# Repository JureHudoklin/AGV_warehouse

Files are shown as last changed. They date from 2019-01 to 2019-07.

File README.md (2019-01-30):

# AGV_warehouse

This is a project I am currently working on. I am working on this also as a final project for my undergraduate degree (diploma). In this project I am developing and programing a robot ("robot platform") that could be used in simulation of a warehouse environment. In a simulation these robots would have to found their way around warehouse based on the input provided by the master computer. Each robot has to follow guiding lines, know his position based on ground markings, be able to autonomously charge itself, stop and report in case of obstacles and load cargo from designated stations. 

I already completed the robot design phase. I have designed the pcb plate as well as the whole assembly. The robot will be assembled in next few weeks when I receive all the necessary parts. This part of the project is located in ./agv-skladiscni-v1/ (KiCad files) and ./Step_modeli/ (step models of robot and pcb plate).

The logic of the robot will run on a BeagleBone blue board. The board will run a ROS operating system. This is the part I have just started working on. I am writing the code in C++ which is the first bigger program I am writing in C++. I expect to learn C++ quite well when I am finished with this project. The code part of this project can be found in the ./catkin_ws/src/ folder. I have not written a lot of code yet bet the currently working part is locate in robot_control package 

**./catkin_ws/src/robot_control/src/...**

<image src="robot_v4/step_modeli/robot_picture.jpg">

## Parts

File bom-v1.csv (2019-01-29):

Refs | Value | Footprint | Quantity | MFR | MPN | SPR | SPN
J4 | I2C | Connector_Wire:SolderWirePad_1x04_P3.175mm_Drill0.8mm | 1 | - | - | - | -
J1 | TOF_0 | Connector_Wire:SolderWirePad_1x05_P3.175mm_Drill0.8mm | 1 | - | - | - | -
J2 | TOF_1 | Connector_Wire:SolderWirePad_1x05_P3.175mm_Drill0.8mm | 1 | - | - | - | -
J5 | ADC | Connector_Wire:SolderWirePad_2x03_P3.175mm_Drill0.8mm | 1 | - | - | - | -
J6 | GP0 | Connector_Wire:SolderWirePad_2x03_P3.175mm_Drill0.8mm | 1 | - | - | - | -
J3 | GP1 | Connector_Wire:SolderWirePad_2x03_P3.175mm_Drill0.8mm | 1 | - | - | - | -
IC1;IC2 | NLAST4051DTR2G | NLAST4051DTR2G:SOP65P640X120-16N | 2 |  | -NLAST4051DTR2G | - | -
U3;U4;U7;U8;U11;U12;U15;U16;U1;U2;U5;U6;U9;U10;U13;U14 | QRE1113GR | OptoDevice:Everlight_ITR8307F43 | 16 | - | -QRE1113GR | - | -
Q1;Q2 | BSS138 | Package_TO_SOT_SMD:SOT-23 | 2 | - | -BSS138 | - | -
R4;R6;R10;R12;R16;R21;R26;R28;R3;R5;R9;R11;R15;R20;R25;R27;R29;R30;R17;R18;R19;R22 | 10K | Resistor_SMD:R_0805_2012Metric_Pad1.15x1.40mm_HandSolder | 22 | - | -CRCW080510K0FKEAC | - | -
R2;R8;R14;R24;R1;R7;R13;R23 | 35R | Resistor_SMD:R_0805_2012Metric_Pad1.15x1.40mm_HandSolder | 8 | - | -ERJ-6ENF35R7V | - | -

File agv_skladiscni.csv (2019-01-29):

Qty | Line Item | Manufacturer | MPN | Octopart URL | Schematic Reference | Internal Part Number | Description | Total Qty (@ Batch Size: 1) | SKU | SKU | SKU | Packaging | Packaging | Packaging | Unit Price (@ Batch Size: 1) | Unit Price (@ Batch Size: 1) | Unit Price (@ Batch Size: 1) | In Stock | In Stock | In Stock | MOQ | MOQ | MOQ | URL | URL | URL | Distributor [Custom] | SKU [Custom] | Packaging [Custom] | Unit Price (@ Batch Size: 1) [Custom] | Line Total [Custom] | Batch Total [Custom] | In Stock [Custom] | MOQ [Custom] | URL [Custom] | Notes
 |  |  |  |  |  |  |  |  | Digi-Key | Arrow Electronics, Inc. | Mouser | Digi-Key | Arrow Electronics, Inc. | Mouser | Digi-Key | Arrow Electronics, Inc. | Mouser | Digi-Key | Arrow Electronics, Inc. | Mouser | Digi-Key | Arrow Electronics, Inc. | Mouser | Digi-Key | Arrow Electronics, Inc. | Mouser
2 | '-NLAST4051DTR2G | ON Semiconductor | NLAST4051DTR2G | https://octopart.com/nlast4051dtr2g-on+semiconductor-445224 |  |  |  | 2 | NLAST4051DTR2GOSCT-ND | NLAST4051DTR2G | NLAST4051DTR2G | Cut Tape | Cut Tape |  | 0.82028697 | 0.4874974282999999 | 0.8026463899999999 | 211 | 1 | 1261 | 1 | 1 | 1 | https://octopart.com/click/track?ak=68b25f31&sig=00cf630&sid=459&ppid=445224&vpid=34062617&ct=offers | https://octopart.com/click/track?ak=68b25f31&sig=09833bd&sid=1106&ppid=445224&vpid=473373786&ct=offers | https://octopart.com/click/track?ak=68b25f31&sig=00e537d&sid=2401&ppid=445224&vpid=116317130&ct=offers | Farnell | 2464612 | Cut Tape | 0.641 | 1.282 | 1.282 | 3755 | 1 | https://octopart.com/click/track?ak=68b25f31&sig=0dc249f&sid=819&ppid=445224&vpid=206199120&ct=offers
16 | QRE1113 | ON Semiconductor | QRE1113 | https://octopart.com/qre1113-on+semiconductor-84331128 |  |  |  | 16 | QRE1113-ND | QRE1113 | QRE1113 | Tube |  |  | 0.792062042 | 0.5158105592 | 0.682690446 | 10991 | 646 | 3394 | 1 | 1 | 1 | https://octopart.com/click/track?ak=68b25f31&sig=0a14e08&sid=459&ppid=84331128&vpid=452472821&ct=offers | https://octopart.com/click/track?ak=68b25f31&sig=092d03a&sid=1106&ppid=84331128&vpid=451899349&ct=offers | https://octopart.com/click/track?ak=68b25f31&sig=0bf3216&sid=2401&ppid=84331128&vpid=438586711&ct=offers | Avnet | QRE1113 |  | 0.4762074571 | 7.6193193136 | 7.6193193136 | 15772 | 1 | https://octopart.com/click/track?ak=68b25f31&sig=06b2d4a&sid=5822&ppid=84331128&vpid=450368001&ct=offers
2 | BSS138 | ON Semiconductor | BSS138 | https://octopart.com/bss138-on+semiconductor-19021258 |  |  |  | 2 | BSS138CT-ND | BSS138 | BSS138 | Cut Tape |  |  | 0.27342899 |  | 0.23814783 | 814070 | 189000 | 13677 | 1 | 3000 | 1 | https://octopart.com/click/track?ak=68b25f31&sig=004b419&sid=459&ppid=19021258&vpid=452459305&ct=offers | https://octopart.com/click/track?ak=68b25f31&sig=05a773f&sid=1106&ppid=19021258&vpid=485898217&ct=offers | https://octopart.com/click/track?ak=68b25f31&sig=0af2366&sid=2401&ppid=19021258&vpid=438580598&ct=offers | ExcessParts.Net | BSS138 |  | 0.11466377 | 0.22932754 | 0.22932754 | 200 |  | https://octopart.com/click/track?ak=68b25f31&sig=03c28bd&sid=13803&ppid=19021258&vpid=81172639&ct=offers
22 | '-CRCW080510K0FKEAC | Vishay | CRCW080510K0FKEAC | https://octopart.com/crcw080510k0fkeac-vishay-23798533 |  |  |  | 22 | 541-3976-1-ND | CRCW080510K0FKEAC | CRCW080510K0FKEAC | Cut Tape | Cut Tape |  | 0.042337392 | 0.0388974789 | 0.074090436 | 2081785 | 509250 | 477454 | 1 | 1 | 1 | https://octopart.com/click/track?ak=68b25f31&sig=0d20d2d&sid=459&ppid=23798533&vpid=454353705&ct=offers | https://octopart.com/click/track?ak=68b25f31&sig=028f037&sid=1106&ppid=23798533&vpid=473524074&ct=offers | https://octopart.com/click/track?ak=68b25f31&sig=030ab9c&sid=2401&ppid=23798533&vpid=454250937&ct=offers | Arrow Electronics, Inc. | CRCW080510K0FKEAC | Cut Tape | 0.0388974789 | 0.8557445358 | 0.8557445358 | 509250 | 1 | https://octopart.com/click/track?ak=68b25f31&sig=028f037&sid=1106&ppid=23798533&vpid=473524074&ct=offers
8 | '-ERJ-6ENF35R7V | Panasonic | ERJ-6ENF35R7V | https://octopart.com/erj-6enf35r7v-panasonic-55422637 |  |  |  | 8 | P35.7CCT-ND | ERJ-6ENF35R7V | ERJ-6ENF35R7V | Cut Tape | Cut Tape |  | 0.0882029 | 0.07938260999999999 | 0.0882029 | 15875 | 4900 | 95993 | 1 | 1 | 1 | https://octopart.com/click/track?ak=68b25f31&sig=09c9812&sid=459&ppid=55422637&vpid=189121626&ct=offers | https://octopart.com/click/track?ak=68b25f31&sig=0660927&sid=1106&ppid=55422637&vpid=473401578&ct=offers | https://octopart.com/click/track?ak=68b25f31&sig=0f0ac6a&sid=2401&ppid=55422637&vpid=195943639&ct=offers | Digi-Key | P35.7CCT-ND | Cut Tape | 0.0882029 | 0.7056232 | 0.7056232 | 15875 | 1 | https://octopart.com/click/track?ak=68b25f31&sig=09c9812&sid=459&ppid=55422637&vpid=189121626&ct=offers
8 | 0854-0-15-20-82-14-11-0 | Mill-Max | 0854-0-15-20-82-14-11-0 | https://octopart.com/0854-0-15-20-82-14-11-0-mill-max-20463977 |  |  |  | 8 | ED1055-ND | 0854-0-15-20-82-14-11-0 | 0854-0-15-20-82-14-11-0 | Bulk |  | Bulk | 0.87320871 | 1.211025817 | 0.87320871 | 112317 | 526 | 0 | 1 | 1 | 1 | https://octopart.com/click/track?ak=68b25f31&sig=0a25628&sid=459&ppid=20463977&vpid=40329792&ct=offers | https://octopart.com/click/track?ak=68b25f31&sig=0bc0763&sid=1106&ppid=20463977&vpid=473313268&ct=offers | https://octopart.com/click/track?c=1&ak=68b25f31&sig=03ae4f1&sid=2401&ppid=20463977&vpid=41065394&ct=offers | Farnell | 2751174 |  | 0.702 | 5.616 | 5.616 | 111 | 1 | https://octopart.com/click/track?ak=68b25f31&sig=03bcc03&sid=819&ppid=20463977&vpid=429766510&ct=offers
1 | BBONE-BLUE | BeagleBoard | BBONE-BLUE | https://octopart.com/bbone-blue-beagleboard-81066055 |  |  |  | 1 |  |  |  |  |  |  |  |  |  |  |  |  |  |  |  |  |  |  | Farnell | 2612583 |  | 69.39 | 69.39 | 69.39 | 2492 | 1 | https://octopart.com/click/track?ak=68b25f31&sig=0b051db&sid=819&ppid=81066055&vpid=423723874&ct=offers
4 | 30:1 MICRO METAL GEARMOTOR MP 6V DUAL | Pololu | 30:1 MICRO METAL GEARMOTOR MP 6V DUAL | https://octopart.com/30%3A1+micro+metal+gearmotor+mp+6v+dual-pololu-75431235 |  |  |  | 4
2 | MICRO METAL GEARMOTOR BRACKET PAIR - WHI | Pololu | MICRO METAL GEARMOTOR BRACKET PAIR - WHI | https://octopart.com/micro+metal+gearmotor+bracket+pair+-+whi-pololu-75442825 |  |  |  | 2
8 | R2-56X3/4 | APM Hexseal | R2-56X3/4 | https://octopart.com/r2-56x3%2F4-apm+hexseal-133757 |  |  |  | 8 |  |  | R2-56X3/4 |  |  |  |  |  | 0.48511595 |  |  | 54 |  |  | 1 |  |  | https://octopart.com/click/track?ak=68b25f31&sig=062e0ba&sid=2401&ppid=133757&vpid=230952262&ct=offers | Mouser | R2-56X3/4 |  | 0.48511595 | 3.8809276 | 3.8809276 | 54 | 1 | https://octopart.com/click/track?ak=68b25f31&sig=062e0ba&sid=2401&ppid=133757&vpid=230952262&ct=offers
2 | SEN-14722 | SparkFun | SEN-14722 | https://octopart.com/sen-14722-sparkfun-93101365 |  |  |  | 2 | 1568-1880-ND | SEN-14722 | SEN-14722 | Bulk |  |  | 19.298794519999998 | 17.596478549999997 | 19.8456525 | 111 | 8 | 22 | 1 | 1 | 1 | https://octopart.com/click/track?c=1&ak=68b25f31&sig=0b0900d&sid=459&ppid=93101365&vpid=485092018&ct=offers | https://octopart.com/click/track?ak=68b25f31&sig=0332f6e&sid=1106&ppid=93101365&vpid=492168591&ct=offers | https://octopart.com/click/track?ak=68b25f31&sig=0545640&sid=2401&ppid=93101365&vpid=486713343&ct=offers | Arrow Electronics, Inc. | SEN-14722 |  | 17.596478549999997 | 35.192957099999994 | 35.192957099999994 | 8 | 1 | https://octopart.com/click/track?ak=68b25f31&sig=0332f6e&sid=1106&ppid=93101365&vpid=492168591&ct=offers
8 | 05.13.253 | Ettinger | 05.13.253 | https://octopart.com/05.13.253-ettinger-5437306 |  |  |  | 8 |  |  |  |  |  |  |  |  |  |  |  |  |  |  |  |  |  |  | element14 APAC | 1466796 |  | 0.4796423356182361 | 3.837138684945889 | 3.837138684945889 | 14871 | 4 | https://octopart.com/click/track?ak=68b25f31&sig=056c70d&sid=11744&ppid=5437306&vpid=132270724&ct=offers
4 | 05.12.103 | Ettinger | 05.12.103 | https://octopart.com/05.12.103-ettinger-5415987 |  |  |  | 4 |  |  |  |  |  |  |  |  |  |  |  |  |  |  |  |  |  |  | element14 APAC | 1466834 |  | 0.28778540137094166 | 1.1511416054837667 | 1.1511416054837667 | 10290 | 4 | https://octopart.com/click/track?ak=68b25f31&sig=01c4ea7&sid=11744&ppid=5415987&vpid=132270698&ct=offers
4 | M2.5 6 PRSTMC Z100 | TR Fastenings | M2.5 6 PRSTMC Z100 | https://octopart.com/m2.5+6+prstmc+z100-tr+fastenings-95659952 |  |  |  | 4 |  |  |  |  |  |  |  |  |  |  |  |  |  |  |  |  |  |  | Farnell | 1420388 |  | 1.17 | 4.68 | 4.68 | 634 | 1 | https://octopart.com/click/track?ak=68b25f31&sig=0602cf9&sid=819&ppid=95659952&vpid=509078641&ct=offers
8 | M3 12 PRSTMC Z100 | TR Fastenings | M3 12 PRSTMC Z100 | https://octopart.com/m3+12+prstmc+z100-tr+fastenings-95659955 |  |  |  | 8 |  |  |  |  |  |  |  |  |  |  |  |  |  |  |  |  |  |  | Farnell | 1420391 |  | 1.24 | 9.92 | 9.92 | 1097 | 1 | https://octopart.com/click/track?ak=68b25f31&sig=05d7318&sid=819&ppid=95659955&vpid=509078647&ct=offers
20 | M3- HFST-Z100- | TR Fastenings | M3- HFST-Z100- | https://octopart.com/m3-+hfst-z100--tr+fastenings-7394229 |  |  |  | 20 |  |  |  |  |  |  |  |  |  |  |  |  |  |  |  |  |  |  | Farnell | 1419447 |  | 0.977 | 19.54 | 19.54 | 3192 | 1 | https://octopart.com/click/track?ak=68b25f31&sig=02b8b90&sid=819&ppid=7394229&vpid=509078655&ct=offers
4 | M2.5- HFST-Z100- | TR Fastenings | M2.5- HFST-Z100- | https://octopart.com/m2.5-+hfst-z100--tr+fastenings-7512629 |  |  |  | 4 |  |  |  |  |  |  |  |  |  |  |  |  |  |  |  |  |  |  | Farnell | 1419446 |  | 1.01 | 4.04 | 4.04 | 1228 | 1 | https://octopart.com/click/track?ak=68b25f31&sig=06cf466&sid=819&ppid=7512629&vpid=509078643&ct=offers
4 | DT000386 | Duratool | DT000386 | https://octopart.com/dt000386-duratool-89505181 |  |  |  | 4 |  |  |  |  |  |  |  |  |  |  |  |  |  |  |  |  |  |  | Newark | 48AC6552 |  | 5.16868994 | 20.67475976 | 20.67475976 | 28 | 1 | https://octopart.com/click/track?ak=68b25f31&sig=0d0659c&sid=2402&ppid=89505181&vpid=477436522&ct=offers
0 | 212X10 | Dremec | 212X10 | https://octopart.com/212x10-dremec-53597534 |  |  |  | 0 |  |  |  |  |  |  |  |  |  |  |  |  |  |  |  |  |  |  | TME | TFM-M2.5X10/DR212 |  |  |  |  | 3170 | 10 | https://octopart.com/click/track?ak=68b25f31&sig=0ad5945&sid=1532&ppid=53597534&vpid=180689506&ct=offers
0 | 213X25 | Dremec | 213X25 | https://octopart.com/213x25-dremec-53597544 |  |  |  | 0 |  |  |  |  |  |  |  |  |  |  |  |  |  |  |  |  |  |  | TME | TFM-M3X25/DR213 |  |  |  |  | 12040 | 10 | https://octopart.com/click/track?ak=68b25f31&sig=0f4a038&sid=1532&ppid=53597544&vpid=180689516&ct=offers
0 | 1874659 | Bossard | 1874659 | https://octopart.com/1874659-bossard-20924902 |  |  |  | 0 |  |  |  |  |  |  |  |  |  |  |  |  |  |  |  |  |  |  | TME | B3/BN117 |  |  |  |  | 245493 | 100 | https://octopart.com/click/track?ak=68b25f31&sig=0f10d11&sid=1532&ppid=20924902&vpid=195120838&ct=offers
0 | M2.5/BN109 | Bossard | M2.5/BN109 | https://octopart.com/m2.5%2Fbn109-bossard-30715687 |  |  |  | 0 |  |  |  |  |  |  |  |  |  |  |  |  |  |  |  |  |  |  | TME | B2.5/BN109 |  |  |  |  | 38815 | 100 | https://octopart.com/click/track?ak=68b25f31&sig=06c4eca&sid=1532&ppid=30715687&vpid=88509478&ct=offers
0 | 1154273 | Bossard | 1154273 | https://octopart.com/1154273-bossard-30713602 |  |  |  | 0 |  |  |  |  |  |  |  |  |  |  |  |  |  |  |  |  |  |  | TME | B3X12/BN384 |  |  |  |  | 8200 | 200 | https://octopart.com/click/track?ak=68b25f31&sig=0083844&sid=1532&ppid=30713602&vpid=88491571&ct=offers
0 | 1135716 | Bossard | 1135716 | https://octopart.com/1135716-bossard-30713551 |  |  |  | 0 |  |  |  |  |  |  |  |  |  |  |  |  |  |  |  |  |  |  | TME | B3X40/BN384 |  |  |  |  | 3200 | 200 | https://octopart.com/click/track?ak=68b25f31&sig=017a52f&sid=1532&ppid=30713551&vpid=88490955&ct=offers
0 | 1154192 | Bossard | 1154192 | https://octopart.com/1154192-bossard-30713592 |  |  |  | 0 |  |  |  |  |  |  |  |  |  |  |  |  |  |  |  |  |  |  | TME | B2.5X6/BN384 |  |  |  |  | 3200 | 200 | https://octopart.com/click/track?ak=68b25f31&sig=060e8c5&sid=1532&ppid=30713592&vpid=88491441&ct=offers

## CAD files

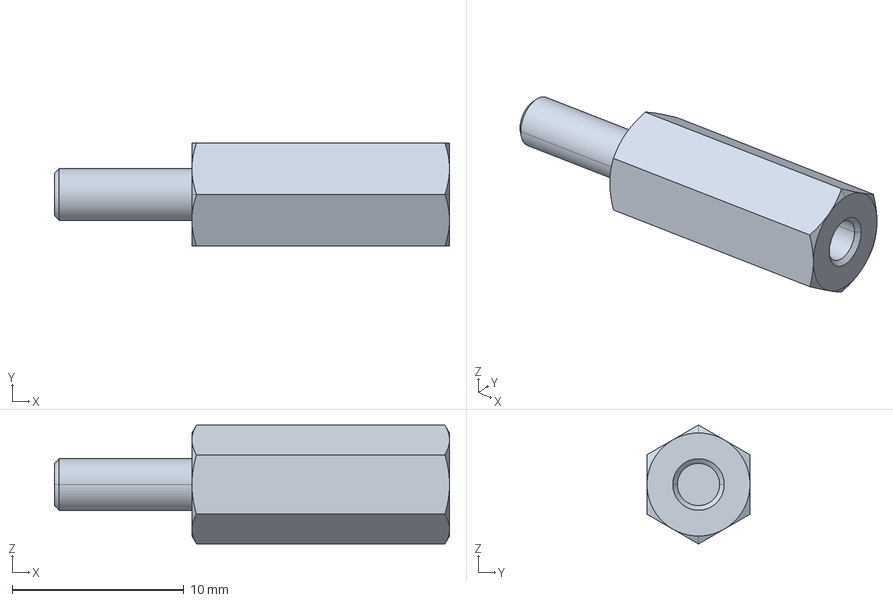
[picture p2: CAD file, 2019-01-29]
robot_v4/step_modeli/pillar_210630060015.stp
23.0 x 6.00 x 6.93 mm

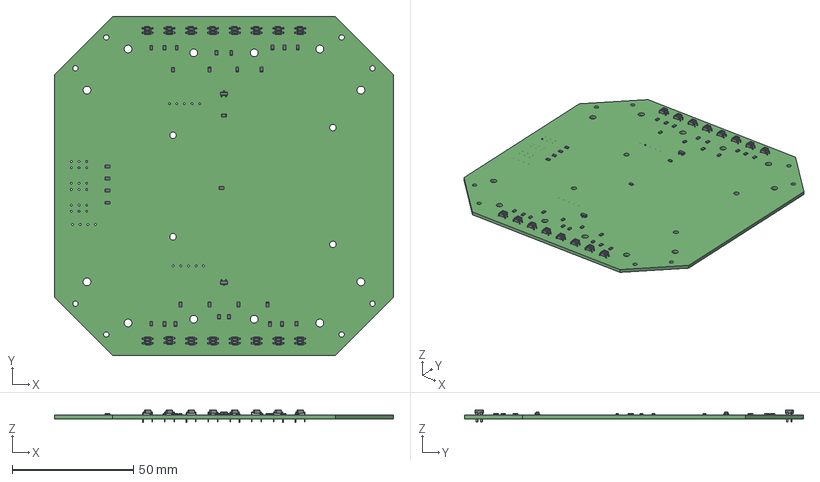
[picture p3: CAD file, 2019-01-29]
robot_v4/step_modeli/agv-skladiscni-v5.step
140.0 x 140.0 x 5.00 mm

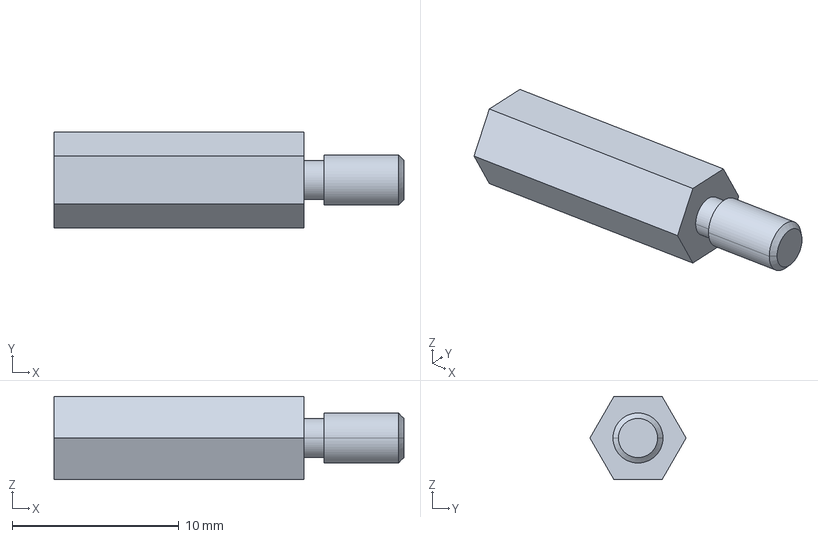
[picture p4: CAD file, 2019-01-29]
robot_v4/step_modeli/yp-515.stp
21.0 x 5.77 x 5.00 mm

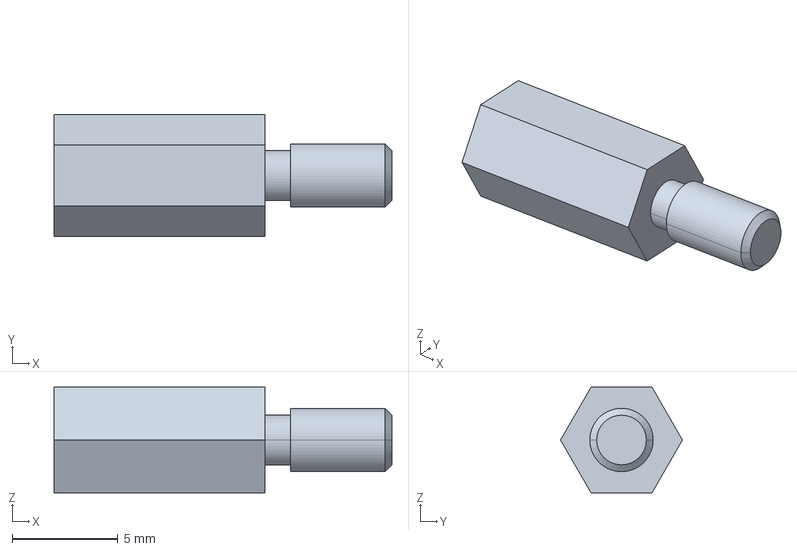
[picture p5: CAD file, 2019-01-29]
robot_v4/step_modeli/yp-510.stp
16.0 x 5.77 x 5.00 mm

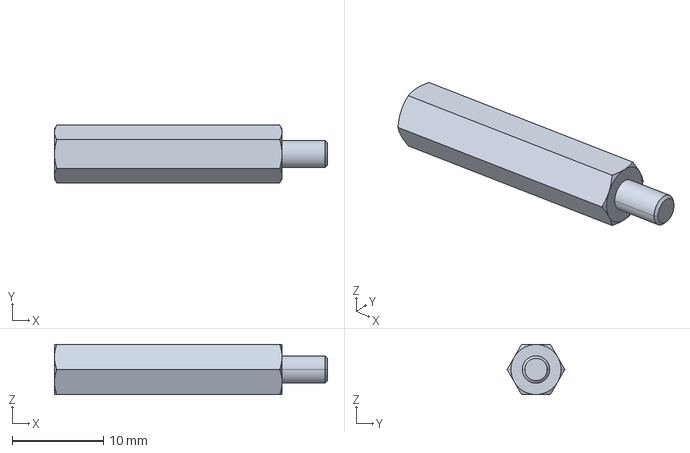
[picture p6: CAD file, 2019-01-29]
robot_v4/step_modeli/3-25-1384848.stp
30.0 x 6.35 x 5.50 mm

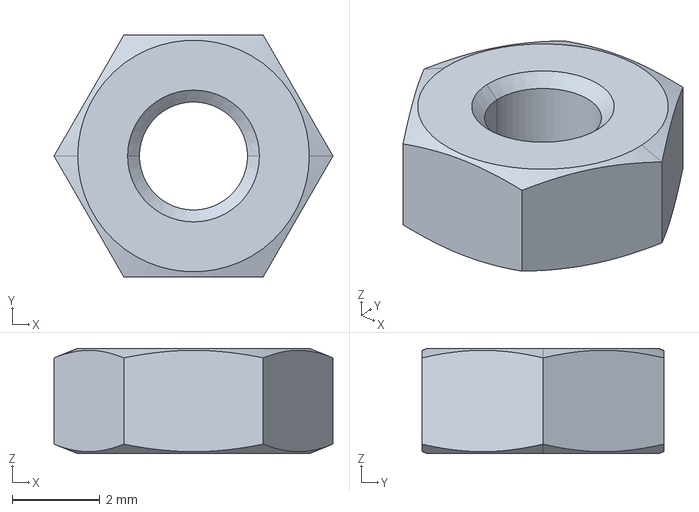
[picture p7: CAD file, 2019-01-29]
robot_v4/step_modeli/nut_din934_m3-6.stp
6.35 x 5.50 x 2.40 mm

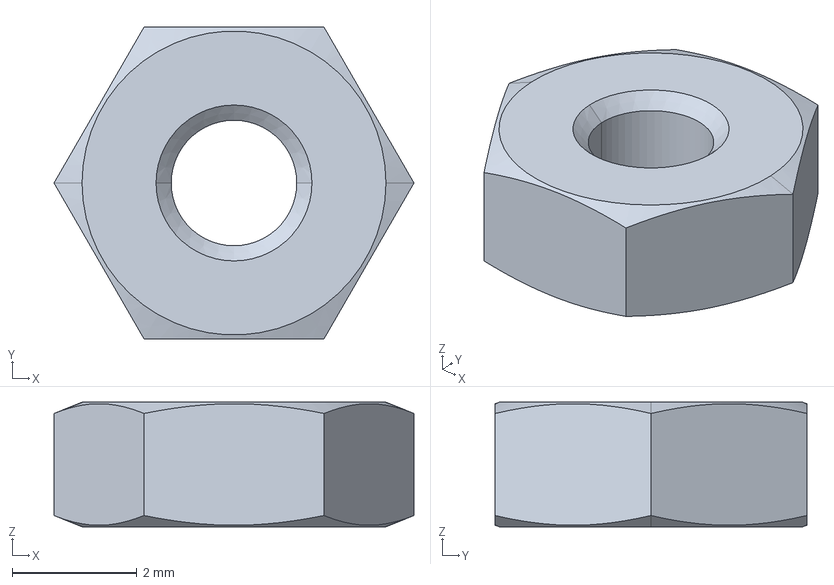
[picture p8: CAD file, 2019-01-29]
robot_v4/step_modeli/nut_din934_m2_5-6.stp
5.77 x 5.00 x 2.00 mm

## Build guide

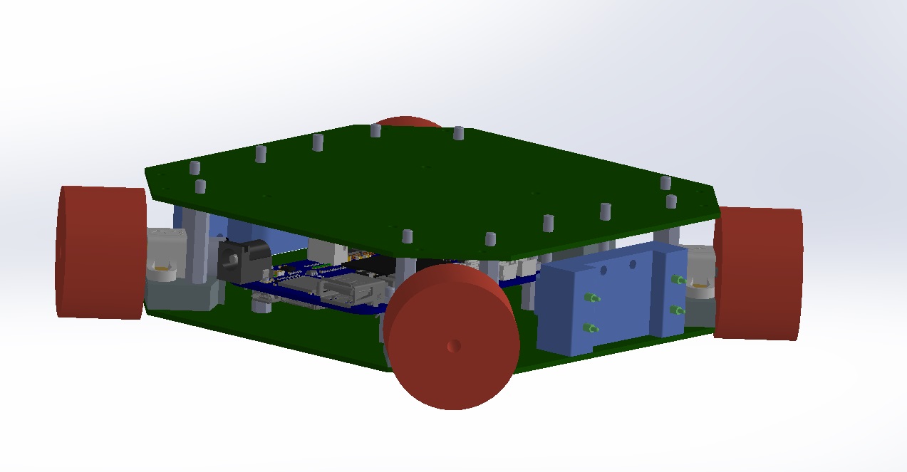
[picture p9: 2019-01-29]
robot_v4/step_modeli/robot_picture.jpg

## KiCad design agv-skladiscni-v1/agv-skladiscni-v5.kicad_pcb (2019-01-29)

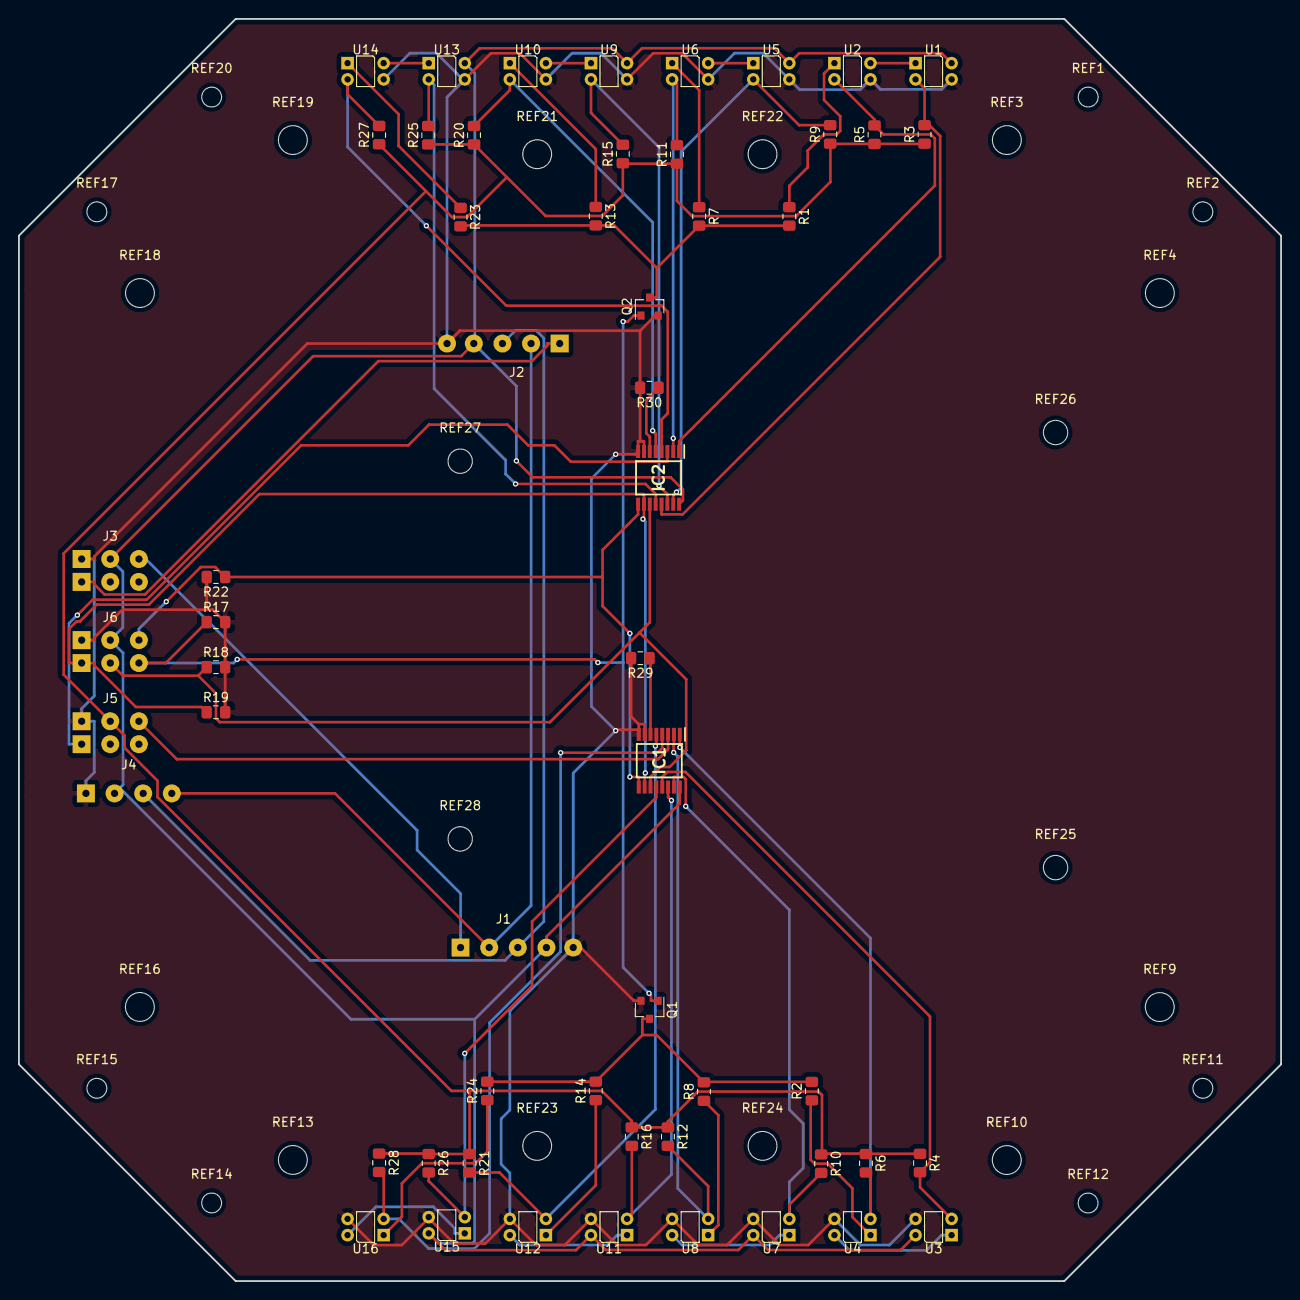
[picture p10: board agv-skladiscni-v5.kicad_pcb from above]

Board: 2 copper layers, 140.0 x 140.0 mm, 80 parts (0 on the bottom side), 49 nets.

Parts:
IC1, IC2: NLAST4051DTR2G; SOP65P640X120-16N
J1: TOF_0; SolderWirePad_1x05_P3.175mm_Drill0.8mm
J2: TOF_1; SolderWirePad_1x05_P3.175mm_Drill0.8mm
J3: GP1; SolderWirePad_2x03_P3.175mm_Drill0.8mm
J4: I2C; SolderWirePad_1x04_P3.175mm_Drill0.8mm
J5: ADC; SolderWirePad_2x03_P3.175mm_Drill0.8mm
J6: GP0; SolderWirePad_2x03_P3.175mm_Drill0.8mm
Q1, Q2: BSS138; SOT-23
R1, R2, R7, R8, R13, R14, R23, R24: 35R; R_0805_2012Metric_Pad1.15x1.40mm_HandSolder
R3, R4, R5, R6, R9, R10, R11, R12, R15, R16, R17, R18, R19, R20, R21, R22, R25, R26, R27, R28, R29, R30: 10K; R_0805_2012Metric_Pad1.15x1.40mm_HandSolder
REF1, REF2, REF11, REF12, REF14, REF15, REF17, REF20 : MountingHole_2.2mm_M2
REF3, REF4, REF9, REF10, REF13, REF16, REF18, REF19, REF21, REF22, REF23, REF24: MountingHole_3.2mm_M3
REF25, REF26, REF27, REF28: MountingHole_2.7mm_M2.5
U1, U2, U3, U4, U5, U6, U7, U8, U9, U10, U11, U12, U13, U14, U15, U16: QRE1113GR; Everlight_ITR8307F43

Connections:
+1V8: J5.2, R3.1, R4.1, R5.1, R6.1, R9.1, R10.1, R11.1, R12.1, R15.1, R16.1, R20.1, R21.1, R25.1, R26.1, R27.1, R28.1
+3V3: IC1.16, IC2.16, J1.4, J2.4, J3.2, J4.2, J6.2, U1.2, U3.2, U5.2, U7.2, U9.2, U11.2, U13.2, U15.2
A0: IC1.3, J5.3
A1: IC2.3, J5.4
DIG0: IC1.9, IC2.9, J6.3, R22.1
DIG1: IC1.10, IC2.10, J6.4, R19.1
DIG2: IC1.11, IC2.11, J6.5, R18.1
GND: IC1.7, IC1.8, IC2.7, IC2.8, J1.5, J2.5, J3.1, J4.1, J5.1, J6.1, Q1.2, Q2.2, R17.2, R18.2, R19.2, R22.2, R29.2, R30.2, U1.4, U2.4, U3.4, U4.4, U5.4, U6.4, U7.4, U8.4, U9.4, U10.4, U11.4, U12.4, U13.4, U14.4, U15.4, U16.4
LED0,1: Q1.3, R2.2, R8.2, R14.2, R24.2
LED10,11: Q2.3, R1.2, R7.2, R13.2, R23.2
LEDS: J6.6, Q1.1, Q2.1, R17.1
unnamed: IC1.6, R29.1
unnamed: IC2.6, R30.1
unnamed: R1.1, U2.1
unnamed: R2.1, U4.1
unnamed: R7.1, U6.1
unnamed: R8.1, U8.1
unnamed: R13.1, U10.1
unnamed: R14.1, U12.1
unnamed: R23.1, U14.1
unnamed: R24.1, U16.1
unnamed: U1.1, U2.2
unnamed: U3.1, U4.2
unnamed: U5.1, U6.2
unnamed: U7.1, U8.2
unnamed: U9.1, U10.2
unnamed: U11.1, U12.2
unnamed: U13.1, U14.2
unnamed: U15.1, U16.2
SCL: J1.3, J2.3, J4.3
SDA: J1.2, J2.2, J4.4
SEN0: IC1.13, R4.2, U3.3
SEN1: IC1.1, R6.2, U4.3
SEN2: IC1.15, R10.2, U7.3
SEN3: IC1.2, R12.2, U8.3
SEN4: IC1.14, R16.2, U11.3
SEN5: IC1.5, R21.2, U12.3
SEN6: IC1.12, R26.2, U15.3
SEN7: IC1.4, R28.2, U16.3
SEN8: IC2.13, R3.2, U1.3
SEN9: IC2.1, R5.2, U2.3
SEN10: IC2.15, R9.2, U5.3
SEN11: IC2.2, R11.2, U6.3
SEN12: IC2.14, R15.2, U9.3
SEN13: IC2.5, R20.2, U10.3
SEN14: IC2.12, R25.2, U13.3
SEN15: IC2.4, R27.2, U14.3
Xshut_0: J1.1, J3.3
Xshut_1: J2.1, J3.4

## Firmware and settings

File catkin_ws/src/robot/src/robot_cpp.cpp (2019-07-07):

// http://mate.tue.nl/mate/pdfs/7566.pdf reference for robot controll
// http://www-ist.massey.ac.nz/conferences/ICARA2004/files/Papers/Paper74_ICARA2004_425_428.pdf
// export ROS_MASTER_URI=http://192.168.43.179:11311 on BBB 192.168.43.179
// export ROS_IP=192.168.43.149 on BBB
// scp -r ubuntu@192.168.7.2:~/catkin_ws/src/ /home/jure/jure_ROS/AGV_warehouse/catkin_ws/

// scp -r /home/jure/jure_ROS/AGV_warehouse/catkin_ws/src/ ubuntu@192.168.7.2:~/catkin_ws/

// IMU filters
// extended calman filter
// https://books.google.si/books?id=68RiDwAAQBAJ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



/*
Encoder: 12CPR
Motor: 50:1
*/

#include <math.h>
#include <ros/ros.h>
//#include <string>
//#include <vector>
#include "robot.h"

#include <robotcontrol.h>

//Messages
#include <std_msgs/Int32.h>
#include <sensor_msgs/Imu.h>
#include <sensor_msgs/MagneticField.h>
#include <sensor_msgs/Range.h>
#include <robot/Line_sensor.h>
#include <robot/coordinate_sys_rotate.h>

#include <geometry_msgs/Twist.h>
#include <nav_msgs/Odometry.h>
#include <tf/transform_broadcaster.h>

// Other
#include <std_srvs/Empty.h>
#include <dynamic_reconfigure/server.h>
#include <robot/ReconfigureConfig.h>

#include <actionlib/client/simple_action_client.h>
#include <actionlib/client/terminal_state.h>
#include <robot/MoveRobotAction.h>
#include <robot/FollowLineAction.h>
//#include <boost/thread.hpp>

#define ANGLE_PER_ENC_PULSE 0.01047197551
#define WHEEL_DIAMETER 38.1
#define DEGREE2RADIANS 0.01745329252

//GPIO setup
#define GP0_4 3, 17
#define GP0_3 3, 20
#define GP0_2 1, 17
#define GP0_1 1, 25

#define GP1_4 2, 3
#define GP1_3 2, 2
#define GP1_2 3, 1
#define GP1_1 3, 2

//Structures
struct Robot_vel_state {
    double target_v[3]; //Is set based on the Koordinate system used (global or robot)
	double actual_v[3]; //Is always the velocity in robot KS
};
struct PID_state {
	double u[3] = {0,0,0};
	double error_1[3] = {0,0,0};
};
struct Robot_enc_val {
	int enc[4];
	ros::Time timestamp;
};
struct PID_koef {
	double P;
	double I;
	double D;
};
struct Vel_Pose {
	double x,y,z;
	double a_x, a_y, a_z;
};



//Publishers
ros::Publisher odom_pub;
ros::Publisher odom_rviz;
nav_msgs::Odometry odom_test;

//Subscribers
ros::Subscriber cmd_vel_sub; 
           
//Services
ros::ServiceServer motors_on; 
ros::ServiceServer motors_off;
ros::ServiceServer follow_line_on;
ros::ServiceServer follow_line_off;
ros::ServiceServer KS_rotate; 



//Define used variable
bool motor_state;
int follow_line = 2;
int use_motors, use_MPU, use_TOF;

//--------------------------TEST_--------------
double power_on_wheel =0.;



//Classes
class Robot {
	private:
		PID_state PID_StateHistory;
		PID_koef PID;
		double scaling_factor;
	public:
		//Initialize
		//Variables
		static double coordinate_ofset;
		ros::Time current_time, last_time;
		static rc_mpu_data_t MPU_data;
		//Structures
		Robot_vel_state robot_vel;
		Robot_enc_val robot_enc_val;
		Vel_Pose vel_pose;
		//Methods
		void set_PID(double p, double i, double d);
		void set_scaling(double i);
		static void dmp_callback(void);
		void read_encoders(Robot_enc_val &old_val);
		void calc_velocities(Robot_enc_val &old_val);
		void weigh_velocities(double(& weighted_velocities)[3]);
		void vel2power(double (&pwr)[4]);
		void wheel_speed(double (&ws)[4] ,double velocities[3]);
};
void Robot::set_PID(double p, double i, double d) {
	PID.P = p;
	PID.I = i;
	PID.D = d;
	return;
}
void Robot::set_scaling(double i) {
	scaling_factor = i;
	return;
}
void Robot::dmp_callback(void) {
	//Add here if any callback is needed after new dmp_data
	return;
}
void Robot::read_encoders(Robot_enc_val &old_val) {
	//Encoders numbered from front left -> counter cloackwise
	for (int i = 0; i<4; i++) {
		old_val.enc[i] = robot_enc_val.enc[i];
	}
	old_val.timestamp = robot_enc_val.timestamp;
	for (int i = 0; i<4; i++) {
		robot_enc_val.enc[i] = rc_encoder_read(i+1);
	}
	robot_enc_val.timestamp = ros::Time::now();
	return;
}
void Robot::calc_velocities(Robot_enc_val &old_val) {
	robot_vel.actual_v[2] = MPU_data.gyro[2] * DEGREE2RADIANS;	// Angular velocity is read directly from gyro

	// In the loop below velocity (mm/s) for each wheel is calculated
	double wheel_vel[4];
	for(int i = 0; i<4; i++) {
		int enc_diff = robot_enc_val.enc[i] - old_val.enc[i];
		double time_diff = robot_enc_val.timestamp.toSec() - old_val.timestamp.toSec();
		wheel_vel[i] = ((double)enc_diff * ANGLE_PER_ENC_PULSE) / time_diff;
		wheel_vel[i] = wheel_vel[i]*WHEEL_DIAMETER / 2.;
	}
	
	
	/*
	Robot velocities are calculated from wheel velocities. As the system of eqations is overdefined,
	method of least squares is used.
	*/


	double pinv_koef = 0.35355339;
	robot_vel.actual_v[0] = pinv_koef * (-wheel_vel[0] - wheel_vel[1] + wheel_vel[2] + wheel_vel[3]);
	robot_vel.actual_v[1] = pinv_koef  * (wheel_vel[0] - wheel_vel[1] - wheel_vel[2] + wheel_vel[3]);


	return;
}
void Robot::wheel_speed(double (&ws)[4], double velocities[3]) {
	for(int i = 0; i<4; i++) {
		double alpha = (M_PI/4.)+(double)i*M_PI/2.;
		double b = 100.;
		ws[i] = (b*velocities[2] - velocities[0] * sin(alpha) + velocities[1]*cos(alpha));
		ws[i] += 50 * getSign<double>(ws[i]);
	}
	return;
}
void Robot::weigh_velocities(double(& weighted_velocities)[3]) {


	double dt = current_time.toSec()-last_time.toSec();
	

	for(int i = 0; i<3; i++) {
		double error;
		double P_, I_, D_;

		// Calculation of current error
		error = robot_vel.target_v[i] - robot_vel.actual_v[i];

		// Proportional part
		P_ = PID.P * error;

		// Integral part with, integrator windup safety
		PID_StateHistory.u[i] += error*dt; 
		
		if (PID_StateHistory.u[i]>300.) {
			ROS_INFO("Integrator windup warning");
			PID_StateHistory.u[i] = 300;
		} else if(PID_StateHistory.u[i]<-300.) {
			ROS_INFO("Integrator windup warning");
			PID_StateHistory.u[i] = -300;
		}
		
		if (PID_StateHistory.u[2]>10.) {
			ROS_INFO("Integrator windup warning");
			PID_StateHistory.u[2] = 10.;
		} else if(PID_StateHistory.u[2]<-10.) {
			ROS_INFO("Integrator windup warning");
			PID_StateHistory.u[2] = -10.;
		}

		I_ = PID.I * PID_StateHistory.u[i];
	
		// Diferential part
		D_ = PID.D * (error-PID_StateHistory.error_1[i])/dt;
		if(D_>150) {
			D_ = 150;
		}
		else if(D_ < -150) {
			D_ = -150;
		}
	

		// Sum of all parts
		weighted_velocities[i] = P_ + I_ + D_;


		// If output is to high signal error and set reference velocity and output to 0
		if (weighted_velocities[i] > 1200) {
			for (int i = 0; i<3; i++) {
				PID_StateHistory.u[i] = 0;
				PID_StateHistory.error_1[i] = 0;
				weighted_velocities[i] = 0;
				robot_vel.target_v[i] = 0;
				ROS_INFO("Control velocity error. Velocity set to 0");
				ROS_INFO("P %f, I %f, D %f", P_, I_, D_);
			}	

			return;
		}
		// Update old error
		PID_StateHistory.error_1[i] = error;
		
	}

	

	return;
}
void Robot::vel2power(double (&pwr)[4]) {
	// We check wheather any velocities are set, if yes integral_on = 1;
	int integral_on = 0;

	for(int i = 0; i<3; i++) {
		if(robot_vel.target_v[i] != 0) {
			integral_on = 1;
		}
	}
	


	// Two tables are created one will be set with calculated velocities form PID and other with wheel speeds
	// based on these velocities.
	double weighted_vel[3] = {0,0,0};
	double wheel_s[4] = {0,0,0,0};

	// If velocities are set calculate new values else just pass 0 to output
	if (integral_on == 1) {
		weigh_velocities(weighted_vel);
		wheel_speed(wheel_s, weighted_vel);
	}
	else {
		for (int i = 0; i<3; i++) {
			PID_StateHistory.u[i] = 0;
			PID_StateHistory.error_1[i] = 0;
		}
	}

	// Set power for each wheel
	for(int i = 0; i<4; i++) {
		pwr[i] = wheel_s[i]/scaling_factor;		//o.1 pwr -> 120mm/s -> 150mm/s x
	}
	return;
}
rc_mpu_data_t Robot::MPU_data;
double Robot::coordinate_ofset = 0;
Robot robot_OBJ;


// Callbacks
void reconfigure_callback(robot::ReconfigureConfig &config, uint32_t level) {

	// Set PID levels to those from reconfigure call
	robot_OBJ.set_PID(config.P_koef, config.I_koef, config.D_koef);

	// Set target velocities to those from reconfigure call
	robot_OBJ.set_scaling(config.sf);
	robot_OBJ.robot_vel.target_v[0] = config.x;
	robot_OBJ.robot_vel.target_v[1] = config.y;
	robot_OBJ.robot_vel.target_v[2] = config.z;
	power_on_wheel = config.x;

	ROS_INFO("%f, %f, %f", config.P_koef, config.I_koef, config.D_koef, config.x);
	return;
}

void twist_callback(const geometry_msgs::Twist &twist) {
	// Update target velocities for the robot
	robot_OBJ.robot_vel.target_v[0] = twist.linear.x;
	robot_OBJ.robot_vel.target_v[1] = twist.linear.y;
	robot_OBJ.robot_vel.target_v[2] = twist.angular.z;
	return;
}

// Action callbacks
void activeCB() {
	// Called once when goal becomes active
	ROS_INFO("Moving robot to new location");
}
void feedbackCB(const robot::MoveRobotFeedbackConstPtr& feedback) {
	for (int i = 0; i<3; i++) {
		robot_OBJ.robot_vel.target_v[i]= feedback->velocity[i];
	}
}
void doneCB(const actionlib::SimpleClientGoalState& state,
			const robot::MoveRobotResultConstPtr& result) {
	
	ROS_INFO("Finished move");
}

void FollowLineActiveCB() {
	// Called once when goal becomes active
	ROS_INFO("Moving robot to new location");
}
void FollowLineFeedbackCB(const robot::FollowLineFeedbackConstPtr& feedback) {
	
}
void FollowLineDoneCB(const actionlib::SimpleClientGoalState& state,
			const robot::FollowLineResultConstPtr& result) {
	
	ROS_INFO("Finished move");
}

// Servic callbacks
bool motors_on_call(std_srvs::Empty::Request &req, std_srvs::Empty::Response &res) {
    motor_state = true;
    return true;
}

bool motors_off_call(std_srvs::Empty::Request &req, std_srvs::Empty::Response &res) {
    motor_state = false;
    return true;
}
bool follow_line_on_call(std_srvs::Empty::Request &req, std_srvs::Empty::Response &res) {
    follow_line = 1;
    return true;
}
bool follow_line_off_call(std_srvs::Empty::Request &req, std_srvs::Empty::Response &res) {
    follow_line = 0;
    return true;
}
bool KS_rotate_call(robot::coordinate_sys_rotate::Request &req,
					robot::coordinate_sys_rotate::Response &res) {

	robot_OBJ.coordinate_ofset = robot_OBJ.MPU_data.fused_TaitBryan[2] + req.KS_offset;
	robot_OBJ.vel_pose.x = req.position[0];
	robot_OBJ.vel_pose.y = req.position[1];

	res.success = 1;

	return true;
}

// Functions

//------------------------------------------------------------------------------------------------------------------//


int main(int argc, char** argv) {
    
    // Define and run the node
	ros::init(argc, argv, "robot");
	ros::NodeHandle nh;

	tf::TransformBroadcaster odom_broadcaster;

	

	// Set node parameters
	nh.getParam("/robot_node/use_motors", use_motors);
	nh.getParam("/robot_node/use_MPU", use_MPU);
	nh.getParam("/robot_node/use_TOF", use_TOF);

	// Set dynamic reconfigure
	dynamic_reconfigure::Server<robot::ReconfigureConfig> server;
	dynamic_reconfigure::Server<robot::ReconfigureConfig>::CallbackType rec_f;
	rec_f = boost::bind(&reconfigure_callback, _1, _2);
	server.setCallback(rec_f);    
	
	// Start services
	motors_on = nh.advertiseService("/motors_on", motors_on_call);
	motors_off = nh.advertiseService("/motors_off", motors_off_call);
	follow_line_on = nh.advertiseService("/follow_line_on", follow_line_on_call);
	follow_line_off = nh.advertiseService("/follow_line_off", follow_line_off_call);
	KS_rotate = nh.advertiseService("/KS_rotate", KS_rotate_call);


	if (use_motors == 1)	{
		ROS_INFO("Initializing motors and encoders");
		cmd_vel_sub = nh.subscribe("/cmd_vel", 10, &twist_callback); 
		if(rc_motor_init() == -1)	{
			ROS_ERROR_STREAM("Motor initialization unsucessfull");
		}
		if(rc_encoder_init() == -1)	{
			ROS_ERROR_STREAM("Encoder initialization unsucessfull");
		}
		for(int i = 1; i<5; i++) {
			if(rc_encoder_write(i, 0) == -1) {
				ROS_ERROR_STREAM("Encoder set 0 unsucessfull");
			}
			else {
				robot_OBJ.robot_enc_val.enc[i] = rc_encoder_read(i);
			}	
		}
		robot_OBJ.robot_enc_val.timestamp = ros::Time::now();
		//cmd_vel_sub = nh.subscribe("/cmd_vel", 1, counterCallback); 
	}
	if (use_MPU == 1) {
		ROS_INFO("Initializing MPU");
		rc_mpu_config_t MPU_conf = rc_mpu_default_config();
		MPU_conf.dmp_fetch_accel_gyro = 1;
		MPU_conf.enable_magnetometer = 1;
		MPU_conf.dmp_sample_rate = 100;
		if(rc_mpu_initialize_dmp(&robot_OBJ.MPU_data, MPU_conf) == -1)	{
			ROS_ERROR_STREAM("MPU initialization unsucessfull");
		}
		robot_OBJ.vel_pose.x = 0;
		robot_OBJ.vel_pose.y = 0;
		robot_OBJ.vel_pose.z = 0;
		robot_OBJ.vel_pose.a_x = 0;
		robot_OBJ.vel_pose.a_y = 0;
		robot_OBJ.vel_pose.a_z = 0;


		odom_pub = nh.advertise<nav_msgs::Odometry>("odom", 10);
		odom_rviz = nh.advertise<nav_msgs::Odometry>("odom_rviz", 10);
		//odom_pub_test = nh.advertise<nav_msgs::Odometry>("odom_2", 10);
		rc_mpu_set_dmp_callback(Robot::dmp_callback);

		ros::Duration(0.5).sleep();
		robot_OBJ.coordinate_ofset = robot_OBJ.MPU_data.fused_TaitBryan[2];


	}

	// Create action client
	
	actionlib::SimpleActionClient<robot::MoveRobotAction> ac("robot_MoveRobot_node");
	ROS_INFO("Waiting for MoveRobot action server to start.");
	ac.waitForServer();
	ROS_INFO("Action server started");
	robot::MoveRobotGoal goal;
	goal.speed = 200.;
	goal.target[0] = 300.;
	goal.target[1] = 0.;
	//ac.sendGoal(goal, &doneCB, &activeCB, &feedbackCB);

	// Create action client
	
	actionlib::SimpleActionClient<robot::FollowLineAction> ac_fl("robot_FollowLine_node");
	ROS_INFO("Waiting for FollowLine action server to start.");
	ac_fl.waitForServer();
	ROS_INFO("Action server started");
	robot::FollowLineGoal goal_fl;


	ros::Rate loop_rate(40);
	
  	robot_OBJ.current_time = ros::Time::now();
  	robot_OBJ.last_time = ros::Time::now();

	Robot_enc_val enc_val_old = {{0,0,0,0},ros::Time::now()};
	while (ros::ok())
	{
		robot_OBJ.last_time = robot_OBJ.current_time;
		robot_OBJ.current_time = ros::Time::now();

		if(follow_line == 1) {
			goal_fl.speed = 150.;
			goal_fl.target_square[0] = 10;
			goal_fl.target_square[1] = 10;
			ac_fl.sendGoal(goal_fl, &FollowLineDoneCB, &FollowLineActiveCB, &FollowLineFeedbackCB);
			follow_line = 2;
		}
		else if (follow_line == 0) {
			ac_fl.cancelAllGoals();
			follow_line = 2;
		}


		if (use_motors) {
			double motor_power[4] = {0,0,0,0};	//Based on v_x,v_y,a_z set power for each motor

			if (motor_state){

				robot_OBJ.read_encoders(enc_val_old);
				robot_OBJ.calc_velocities(enc_val_old);
				robot_OBJ.vel2power(motor_power);

				  
				for(int i = 0; i<4; i++) {
					double m;
					m = motor_power[i];
					if(m > 0.6 || m<-0.6) {
						m = 0.;
						ROS_INFO("wheel %d, power EXCEED", i);
						ROS_INFO("motor_power: %f", motor_power[i]);
						ROS_INFO("robot_vel x: %f", robot_OBJ.robot_vel.actual_v[0]);
						ROS_INFO("robot_vel y: %f", robot_OBJ.robot_vel.actual_v[1]);
					}
					rc_motor_set(i+1, -m);
				}
			}
			else {
				rc_motor_set(1,0);
				rc_motor_set(2,0);
				rc_motor_set(3,0);
				rc_motor_set(4,0);
			}
		}



		if (use_MPU) {
			//http://wiki.ros.org/navigation/Tutorials/RobotSetup/Odom
			double dt = (robot_OBJ.current_time - robot_OBJ.last_time).toSec();

			//Calculater move change in x,y coordina. Angle is set based on gyro.
			robot_OBJ.vel_pose.a_z = robot_OBJ.MPU_data.fused_TaitBryan[2];
			
			double dh = robot_OBJ.vel_pose.a_z - robot_OBJ.coordinate_ofset;
			
			double delta_x = (robot_OBJ.robot_vel.actual_v[0]*cos(dh) - robot_OBJ.robot_vel.actual_v[1]*sin(dh))*dt;
			double delta_y = (robot_OBJ.robot_vel.actual_v[0]*sin(dh) + robot_OBJ.robot_vel.actual_v[1]*cos(dh))*dt;

			geometry_msgs::Quaternion odom_quat;
			//Save position changes to robot object
			robot_OBJ.vel_pose.x += delta_x;
			robot_OBJ.vel_pose.y += delta_y;

			
			//Create quaternion from gyro + ofset for robot
			odom_quat = tf::createQuaternionMsgFromYaw(dh);

			//Pupulate odom_trans
			geometry_msgs::TransformStamped odom_trans;
			odom_trans.header.stamp = robot_OBJ.current_time;
			odom_trans.header.frame_id = "global";
			odom_trans.child_frame_id = "robot";

			odom_trans.transform.translation.x = robot_OBJ.vel_pose.x/1000;
			odom_trans.transform.translation.y = robot_OBJ.vel_pose.y/1000;
			odom_trans.transform.translation.z = 0.0;
			odom_trans.transform.rotation = odom_quat;

			//Brodcast transform
			odom_broadcaster.sendTransform(odom_trans);

			//next, we'll publish the odometry message over ROS
			nav_msgs::Odometry odom;
			odom.header.stamp = robot_OBJ.current_time;
			odom.header.frame_id = "global";

			//Set the position
			odom.pose.pose.position.x = robot_OBJ.vel_pose.x;
			odom.pose.pose.position.y = robot_OBJ.vel_pose.y;
			odom.pose.pose.position.z = 0.0;
			odom.pose.pose.orientation = odom_quat;

			//Set the velocity
			odom.child_frame_id = "robot";
			odom.twist.twist.linear.x = robot_OBJ.robot_vel.actual_v[0];
			odom.twist.twist.linear.y = robot_OBJ.robot_vel.actual_v[1];
			odom.twist.twist.angular.z = robot_OBJ.robot_vel.actual_v[2];
 
			//Publish the message
			odom_pub.publish(odom);
			odom.pose.pose.position.x = robot_OBJ.vel_pose.x/1000;
			odom.pose.pose.position.y = robot_OBJ.vel_pose.y/1000;

			odom_rviz.publish(odom);


		}	
		ros::spinOnce();
		loop_rate.sleep();
	}


	ROS_INFO("Running device cleanup");
	if (use_motors){
		rc_motor_cleanup();
		rc_encoder_cleanup();
	}
	if (use_MPU){
		rc_mpu_power_off();
	}
	

	return 0;
}

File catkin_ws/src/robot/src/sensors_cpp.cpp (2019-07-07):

#include <math.h>
#include <ros/ros.h>
#include <string>
#include <vector>

#include <robotcontrol.h>
#include "vl53l0x.h"
#include "robot.h"

//Messages
#include <std_msgs/Int32.h>
#include <sensor_msgs/Imu.h>
#include <sensor_msgs/MagneticField.h>
#include <sensor_msgs/Range.h>
#include <robot/Control.h>
#include <robot/Line_sensor.h>
#include <robot/coordinate_sys_rotate.h>

#include <geometry_msgs/Twist.h>
#include <geometry_msgs/PolygonStamped.h>
#include <nav_msgs/Odometry.h>
#include <tf/transform_broadcaster.h>

#include <std_srvs/Empty.h>
#include <dynamic_reconfigure/server.h>
#include <robot/ReconfigureConfig.h>

#define DEGREE2RADIANS 0.01745329252
#define DISTANCE_BETWEEN_SENSORS 9


//GPIO setup
#define GP0_1 3, 17 //LED_S
#define GP0_2 3, 20 //DIG 2
#define GP0_3 1, 17 //DIG 1
#define GP0_4 1, 25 //DIG 0

#define GP1_4 2, 3
#define GP1_3 2, 2
#define GP1_2 3, 1
#define GP1_1 3, 2

float* calculateLinePosition(double* front_sen, double* back_sen) {
        float* line_pos = new float[2];

        int f = getMinIndex<double>(front_sen+1, 6)+1;
        int b = getMinIndex<double>(back_sen+1, 6)+1;

        double f_v, b_v;

        f_v = -(f-3.5) - 0.33*(front_sen[f-1] - front_sen[f+1]);    
        b_v = -(b-3.5) - 0.33*(back_sen[b-1] - back_sen[b+1]);

        line_pos[0] = DISTANCE_BETWEEN_SENSORS * (float)f_v;

        line_pos[1] = DISTANCE_BETWEEN_SENSORS * (float)b_v;

        return line_pos;
}

//Publishers
ros::Publisher line_sen_pub; // topic = line_sen
ros::Publisher line_sen_pos_pub;
ros::Publisher tof_pub;

int use_line;
int use_TOF;

VL53L0X vl53l0x;

int main(int argc, char** argv) {


    //Definer and run the node
    ros::init(argc, argv, "robot_sensors_node");
	ros::NodeHandle nh;
    tf::TransformBroadcaster tof_broadcaster;

    //Set node parameters
    nh.getParam("/robot_sensors_node/use_line", use_line);
    nh.getParam("/robot_sensors_node/use_TOF", use_TOF);

    ROS_INFO("Starting robot_sensors");


    if (use_line) {
		ROS_INFO("Initializing line senzors");
        rc_adc_init();
        rc_gpio_init(GP0_1, GPIOHANDLE_REQUEST_OUTPUT); //LED_S
        rc_gpio_init(GP0_2, GPIOHANDLE_REQUEST_OUTPUT); //DIG_2
        rc_gpio_init(GP0_3, GPIOHANDLE_REQUEST_OUTPUT); //DIG_1
        rc_gpio_init(GP0_4, GPIOHANDLE_REQUEST_OUTPUT); //DIG_0

        line_sen_pub = nh.advertise<robot::Line_sensor>("/line_sen", 1);
        line_sen_pos_pub = nh.advertise<geometry_msgs::PolygonStamped>("/line_pos", 1);
    }
    // ToF init
    if (use_TOF)
    {
        ROS_INFO_STREAM("Initializing ToF...");
        tof_pub = nh.advertise<sensor_msgs::Range>("tof/range", 10);
        if (vl53l0x.init())
        {
            ROS_INFO_STREAM("ToF initialized");
            vl53l0x.startContinuous();
        }
        else
        {
            ROS_ERROR_STREAM("failed to initialize TOF");
            return -1;
        }
    }
       

    //Set time variables and ros loop rate
    ros::Time current_time, last_time;
    current_time = ros::Time::now();
    last_time = ros::Time::now();
    ros::Rate loop_rate(30);

    while (ros::ok())
	{
        last_time = current_time;
        current_time = ros::Time::now();
        
        if (use_line) {
            double line_values_f[8];
            double line_values_b[8];
            robot::Line_sensor line_sen_msg;
            geometry_msgs::PolygonStamped line;


            for(int j = 0; j<2; j++) {
                rc_gpio_set_value(GP0_1, j); //LED_S
                ros::Duration(0.001).sleep();


                for(int i = 0; i<8; i++) {
                    int a, b, c;
                    a = i & 0b001;
                    b = i & 0b010;
                    c = i & 0b100;
                    rc_gpio_set_value(GP0_4, a);    //DIG_0
                    rc_gpio_set_value(GP0_3, b);    //DIG_1
                    rc_gpio_set_value(GP0_2, c);    //DIG_2

                    ros::Duration(0.001).sleep(); //Sleeps so that multiplexer has time to settle

                    if (j == 0) {
                        line_values_f[i] = rc_adc_read_volt(1);
                        //ros::Duration(0.005).sleep();
                        line_values_b[i] = rc_adc_read_volt(3);
                    }
                    else {
                        line_values_f[i] = -rc_adc_read_volt(1)+line_values_f[i];
                        //ros::Duration(0.005).sleep();
                        line_values_b[i] = -rc_adc_read_volt(3)+line_values_b[i];
                    }
                }
            }
            rc_gpio_set_value(GP0_4, 0);
            double sum_f, sum_b; // Use this to determine if no line is detected or all sensors are on line

			for (int i = 0; i<8; i++) {
				line_sen_msg.front_sensors[i] = line_values_f[i];
				line_sen_msg.back_sensors[i] = line_values_b[i];
                sum_f += line_values_f[i];
                sum_b += line_values_b[i];
			}
            
            float* line_position;

            /* Add here an if statemen to see if no line is detected or all sensors on line */


            line_position = calculateLinePosition(line_values_f, line_values_b); // Line Position is calculated

            geometry_msgs::Point32 p_f;
            geometry_msgs::Point32 p_f_2; // This point only to show in RViz
            geometry_msgs::Point32 p_b;
            geometry_msgs::Point32 p_b_2; // This point only to show in RViz


            p_f.x = 0.2;
            p_f.y = line_position[0]/1000;
            p_f.z = 0;

            p_f_2.x = 0.2;
            p_f_2.y = line_position[0]/1000 +0.03;
            p_f_2.z = 0;

            p_b.x = -0.2;
            p_b.y = line_position[1]/1000;
            p_b.z = 0;

            p_b_2.x = -0.2;
            p_b_2.y = line_position[1]/1000 +0.03;
            p_b_2.z = 0;

            line.polygon.points.push_back(p_f);
            line.polygon.points.push_back(p_f_2);   // RViz
            line.polygon.points.push_back(p_b_2);   // RViz
            line.polygon.points.push_back(p_b);

            line_sen_msg.time_stamp = current_time;
            line.header.stamp = current_time;
            line.header.frame_id = "robot";

			line_sen_pub.publish(line_sen_msg);	
            line_sen_pos_pub.publish(line);	
            

            delete[] line_position;	
        }

        if (use_TOF)
        {


            //Pupulate tof_trans
			geometry_msgs::TransformStamped tof_trans;
			tof_trans.header.stamp = current_time;
			tof_trans.header.frame_id = "robot";
			tof_trans.child_frame_id = "tof";

			tof_trans.transform.translation.x = 0.07;
			tof_trans.transform.translation.y = 0;
			tof_trans.transform.translation.z = 0.02;
			tof_trans.transform.rotation.x = 0;
            tof_trans.transform.rotation.y = 0;
            tof_trans.transform.rotation.z = 0;
            tof_trans.transform.rotation.w = 1;

			//Brodcast transform
			tof_broadcaster.sendTransform(tof_trans);
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

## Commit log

2019-02-16 Robot calculate velocities
2019-02-19 PID controls for velocities
2019-02-19 PID controler
    [Reconfigure.cfg]
2019-02-27 Removed error in gpio setup
    [robot_cpp.cpp]
2019-03-12 PID change
    [Reconfigure.cfg]
2019-03-12 Control changes
    [Reconfigure.cfg]
2019-03-12 PID working
2019-04-09 Changes to CMakeFIle, Finished MoveRobot action server, started on Ac…
2019-04-09 Small error corections
    [Reconfigure.cfg]
2019-04-28 Changes to MoveRobot bug fixes
    [robot_cpp.cpp]
2019-05-01 MoveRobot working
    [Reconfigure.cfg]
2019-05-11 changed to Velocity PID with FeedForward
    [Reconfigure.cfg, agv-skladiscni-v5.sch]
2019-05-12 Fixed errors in new PID control. Calibrated PID control settings. Need to add anti integrator winduip in PID
    [Reconfigure.cfg]
2019-06-17 Sensors error fixes
2019-06-18 FollowLine acition dela, popravljen PID spet dela, potrebno se nastaviti koeficiente, odstrani vse dodane ROS_INFO za testiranje
    [Reconfigure.cfg]
2019-06-19 Some code cleanup
    [Reconfigure.cfg]
2019-06-19 Corrected an error in robot move and robot position calculation. Set new koeficients for file follow
    [robot_cpp.cpp]
2019-07-07 Some cleanup
    [Reconfigure.cfg]
